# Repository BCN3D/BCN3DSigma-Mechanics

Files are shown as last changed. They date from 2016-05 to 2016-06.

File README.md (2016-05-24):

## What’s hold in this repository?
This repository will hold all the information about the Mechanics of the BCN3D Sigma.
As a declared Open Source organization, it's in our mission to release all the original design files to you to be able to learn, reuse and improve. Open Source not only means code, it also concerns hardware.

We’ve managed to design and manufacture the BCN3D Sigma thanks to our previous experience in the 3D printing industry, the ideas coming from the community, our engineering background and a narrow collaboration with our suppliers. Our goal is justify the decisions we took and share the know-how we acquired so far.

We also provide the source files for those who want to check the core of the BCN3D Sigma. You can consult both the CAD files and the technical drawings.

## CONCEPT DESIGN
During the concept design stage we set a clear target which determined the whole design and decisions: The BCN3D Sigma is a professional printer.

### Aesthetics
It has to look  like a professional equipment. Our previous printers were made with aluminium extruded profiles and plastic printed parts. That made sense for printers oriented to makers or schools, sold as a kit. But, in this case, aesthetic was a major player. For this reason, we adopted a welded aluminium frame, which allows the Sigma to be a unique and attractive 3D printer

### Multimaterial
As a professional printer, it has to print as many materials as possible. Not only for engineers, who require tough -or flexible-, functional polymers, but also for designers who need the aesthetic component. However, material is not the only limitation. Complex geometries, overhangs and 3D printing doesn’t get along. So we wanted the Sigma to be a real solution for those users who need to print with supports as a must. In conclusion, the Sigma is the first and only commercial 3D printer with an Independent Dual Extuder (IDEX) system, which avoid all the side problems dual extrusion may cause.

### High Quality
The 3D Printing industry is maturing. Users are more and more demanding and 3D printing must be a solution, not a headache. For this reason, the Sigma has to be a reliable piece of engineering, easy to assemble, maintain and capable to print seamlessly high quality objects, no matter how complex they are.

### High Capacity
Real-life and functional parts are not always small. A big printing volume is a great advantage for a professional 3D Printer although the Sigma intends to be a desktop-sized printer. Allocating all the items and devices inside the frame, while granting ease-to-use and optimizing the axes structure were a key goal.

## DETAIL DESIGN INSIGHTS

We faced dozens of challenges during the design process. Below we describe some of them:

### Frame
Probably the biggest challenge. First we thought in a chassis made of profiles and then cover it. But then realized the cost in materials for that solution would be high enough to look for alternatives that could contribute more in the aesthetic field, even that could be a bit more expensive. On the other side, we wanted the Sigma to be an accessible printer, wide and open in order to ease the handling and operation. So we decided to explore the option of designing a unibody frame where all the mechanical components were mounted on and with a wide frontal oberture.

First we had to decide between using aluminium or steel. Steel offers many advantages: It’s a very stiff metal, great to build structures and precise mechanical systems. In addition, it’s easy to work with and cheap. But it’s -really- heavy. We contemplated the option of using a thinner metal sheet of steel for the frame. After ordering a prototype, we dismissed the idea, though. Still it had a great mechanical behaviour and a relative low weight, the feeling of touching a thin metal sheet (1.5mm) was unpleasant because it felt like a cutting edge. And it didn’t look sturdy. So to achieve both a reliable look and a pleasant contact, we needed to go up to 3mm thickness. But then the shipping costs would be absurdly high and the handling, a constant hassle -both during the assembly process and for the final user.

Aluminium, on the other hand, provides lightness and a smooth and sturdy look. But it’s more expensive as a material and it’s harder to laser cut and weld. After balancing pros and cons, we bet on aluminium option -although we had a plan B.

The second big issue to manage was the manufacturing process. We contemplated two different ways to do it: either manufacture the frame by parts and screw them all together in the assembly line or weld the frame. Welding aluminium is hard and the welding process itself has some thermal and geometric implications that have to be considered. But it allows to reduce the assembling time dramatically while it outsources a key process.

As alternative, designing the frame as separate parts to screw together was considerably cheaper - as you save a handmade process such as welding and polishing. But the assembling of the frame and adjustment could be very delicate and incompatible with our production tag time. So the overall cost wouldn’t be that different in both options. The aesthetic component, though, would be very penalized with this alternative, because we would need to add dozens of screws on the frame.

For these reasons, we finally opted for a welded structure. We sat hours with our supplier discussing the best way to design every single part in order to grant a proper alignment between the faces that would hold the axes. Furthermore, we also studied the mechanical behaviour of the frame with some CAE studies, simulating stress and deformations during a standard usage.

### High quality components
A good frame is not enough to achieve amazing results. In such a precision equipment as the Sigma, all the mechanical components play a key role. Due to the product requirements in terms of size and use of the internal space of the printer we had, we opted for a axes structure with the toolheads moving in the XY plane and an up and down moving Z axis.

With the XY plane decided to mount high precision linear guides. Despite its cost slightly higher than a system based on rods and bearings, the linear rails offer a professional look, an easy assembling and a compact package.

Regarding the Z axis, we were aware of the importance to have a robust guide system in order to avoid classic artifacts in printed parts related with a bad Z performance, such as Z wobbling. We also had experience using couplings and to connect the actuator with the leadscrew and we knew that a bad assembling could cause poor quality results. With this background, we chose using Ø12mm guide rods and a stepper motor with an inserted leadscrew. The whole system provides a high repeatability and accuracy.

### Independent Dual Extrusion
A 3D printer with such an specific feature increases the design unknowns and multiplies the components. Not only the firmware and the electronics need to be highly customized, but also mechanically there are some decisions to take.

First of all, because of the multiple components to hold, the internal parts tend to be more complex than other printers. So we decided to use aluminium sheet bending technology to manufacture the inner parts. As the manufacturing tolerances are acceptable for the purposes we intend and the technology is cheap and easily scalable, we considered the technology optimum.  

Two independent Extruders means have an extra moving stepper for the second toolhead, and the extra toolhead itself. On the other hand, when printing with both extruders it’s important to have a bucket to purge the idle hotends before start printing the model again. All this parts add weight to a moving element, which is a problem to print fast because the high inertias may worsen the print quality. So we designed the X and Y Axis as light as possible, saving as many grams as possible with every single component. Not only weight is important when doubling the toolheads, but also space. So we decided to adopt a bowden-based feeding system and miniaturize all the items as much as possible.

### Big Printing Volume
The BCN3D Sigma features 210x297x210mm printing volume. In order to provide such a big volume and a free space on both sides to park the idle toolhead, but still having a desktop-sized printer, we had to reorient the Z platform. The main issue to solve, though, was granting the stiffness of the structure with a big overhang of more than 300mm.

To prevent vibrations, we adopted high quality bearings with low clearance and we designed and  simulated a custom metal sheet structure, which allows to get a great quality prints with a smooth surface despite the big overhang.

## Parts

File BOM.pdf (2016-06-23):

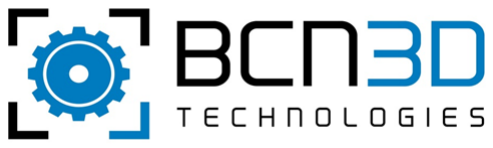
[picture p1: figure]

# | N/referencia S/referencia | Descripció | Unitats/kit | Proveïdor

1 | 10082 | CU03 | Cable USB 2.0 1,8m | 1 | CABLEMATIC
2 | 10210 | | SD Card 8GB | 1 | RS AMIDATA
3 | 10988 | | PLA 3mm 0,5kg JET BLACK STARTER KIT | 1 | BBOLID, S.L.
4 | 10989 | | PLA 3mm 0,5kg ARCTIC WHITE STARTER KIT | 1 | BBOLID, S.L.
5 | 10273 | FA80 | Cable alimentación IEC 1,5m | 1 | CABLEMATIC
6 | 10446 | Q34 | Pulley GT2, 20 Teeth 5mm Bore | 2 | JINAN YUKI INTERNATIONAL TRADE CO., LTD
7 | 10476 | | USB Cable Extension | 1
8 | 10616 | 145 | 3D Lac | 1 | LEÓN 3D IMPRESIÓN
9 | 10628 | P71 | Extruder Thermistor Wired | 2 | KUONGSHUN ELECTRONIC LIMITED
10 | 10826 | 15129 | Patas para tornillo 7,1x15,9mm | 4 | ESSENTRA COMPONENTS S.L.U
11 | 10827 | BCN3DSigma‐M01C00.0P000 | BCN3DSigma‐Structure | 1 | FARGUELL
12 | 10828 | BCN3DSigma‐M05C02.0P01D | BCN3DSigma‐Stepper Holder Right | 1 | FARGUELL
13 | 10829 | BCN3DSigma‐M05C01.0P02D | BCN3DSigma‐Stepper Holder Left | 1 | FARGUELL
14 | 10830 | BCN3DSigma‐M05C01.0P03D | BCN3DSigma‐X Axis Idler | 2 | FARGUELL
15 | 10831 | BCN3DSigma‐M05C01.0P01C | BCN3DSigma‐Belt Clamp | 2 | FARGUELL
16 | 10832 | | BCN3DSigma‐Upper Platform | 1 | FARGUELL
17 | 10833 | BCN3DSigma‐M03C01.0P01D | BCN3DSigma‐Lower Platform | 1 | FARGUELL
18 | 10834 | BCN3DSigma‐M03C01.0P02C | BCN3DSigma‐Reinforcement | 1 | FARGUELL
19 | 10835 | BCN3DSigma‐M06C01.0P05E | BCN3DSigma‐Lower Cover | 2 | FARGUELL
20 | 10836 | BCN3DSigma‐M06C01.0P06D | BCN3DSigma‐Upper Cover | 2 | FARGUELL
21 | 10837 | BCN3DSigma‐M06C01.0P07C | BCN3DSigma‐Hotend Plate | 2 | FARGUELL
22 | 10838 | BCN3DSigma‐M02C01.0P06B | BCN3DSigma‐Y Axis Idler | 2 | FARGUELL
23 | 10839 | BCN3DSigma‐M01C01.0P05C | BCN3DSigma‐Y Idler Tensioner | 2 | FARGUELL
24 | 10840 | BCN3DSigma‐M01C01.0P07B | BCN3DSigma‐Guide Spacer | 2 | FARGUELL
25 | 10841 | BCN3DSigma‐M01C01.0P15A | BCN3DSigma‐Square 90 | 8 | RIERA I TUTÓ
26 | 10842 | BCN3DSigma‐M01C01.0P16A | BCN3DSigma‐Square 60 | 2 | RIERA I TUTÓ
27 | 10843 | BCN3DSigma‐M04C02.0P01C | BCN3DSigma‐SD Holder | 1 | FARGUELL
28 | 10844 | BCN3DSigma‐M04C01.0P02B | BCN3DSigma‐Screen Bezel | 1 | FARGUELL
29 | 10845 | BCN3DSigma‐M08C01.0P02A | BCN3DSigma‐Spool Support | 2 | FARGUELL
30 | 10846 | BCN3DSigma‐M05C03.0P02A | BCN3DSigma‐X Support | 2 | FARGUELL
31 | 10847 | BCN3DSigma‐M05C03.0P03A | BCN3DSigma‐Connection plate | 2 | FARGUELL
32 | 10848 | BCN3DSigma‐M05C03.0P01A | BCN3DSigma‐X Reinforcement | 1 | FARGUELL
33 | 10849 | BCN3DSigma‐M05C01.0P06C | BCN3DSigma‐Purger Base Left | 1 | FARGUELL
34 | 10850 | BCN3DSigma‐M05C02.0P02C | BCN3DSigma‐Purger Base Right | 1 | FARGUELL
35 | 10851 | BCN3DSigma‐M06C01.0P08D | BCN3DSigma‐X Plate Left | 1 | FARGUELL
36 | 10852 | BCN3DSigma‐M06C02.0P01D | BCN3DSigma‐X Plate Right | 1 | FARGUELL
37 | 10853 | BCN3DSigma‐M06C01.0P04C | BCN3DSigma‐Connection Board Support | 2 | FARGUELL
38 | 10854 | BCN3DSigma‐M02C02.0P01C | BCN3DSigma‐Y Stepper Holder | 1 | FARGUELL
39 | 10855 | BCN3DSigma‐M07C01.0P05C | BCN3DSigma‐Extruder Stepper Holder | 2 | FARGUELL
40 | 10856 | BCN3DSigma‐M07C01.0P03A | BCN3DSigma‐Extruder Plate MK8 | 2 | FARGUELL
41 | 10857 | VIDRIO MATE 4, 212X300mm | Vidrio Mate 4, 212x300mm, 0,5mm canto biselado | 1 | DISOLGLASS, S.L.
42 | 10858 | FFC1.00A15/1151M4.0‐4.0‐08.0‐0 | BCN3DSigma‐Cable FFC X1 Motor | 1 | AXON' CABLE S.A.S.
43 | 10859 | FFC1.00A15/1151M4.0‐4.0‐08.0‐0 | BCN3DSigma‐Cable FFC X0 Motor | 1 | AXON' CABLE S.A.S.
44 | 10860 | FFC1.00A15/0159M4.0‐4.0‐08.0‐0 | BCN3DSigma‐Cable FFC Z Motor | 1 | AXON' CABLE S.A.S.
45 | 10861 | FFC1.00A15/0750M4.0‐4.0‐08.0 | BCN3DSigma‐Cable FFC Y Motor | 1 | AXON' CABLE S.A.S.
46 | 10862 | FFC1.00A15/0561M4.0‐4.0‐08.0 | BCN3DSigma‐Cable FFC Extruder 1 | 1 | AXON' CABLE S.A.S.
47 | 10863 | FFC1.00A15/0561M4.0‐4.0‐08.0 | BCN3DSigma‐Cable FFC Extruder 0 | 1 | AXON' CABLE S.A.S.
48 | 10864 | FFC1.00D20/1439M5.0‐5.0‐08.0 | BCN3DSigma‐Cable FFC Hotend 0 | 1 | AXON' CABLE S.A.S.
49 | 10865 | FFC1.00D20/1439M5.0‐5.0‐08.0 | BCN3DSigma‐Cable FFC Hotend 1 | 1 | AXON' CABLE S.A.S.
50 | 10866 | BCN3DSigma‐M09C00.0P09B | BCN3DSigma‐Cable Hotbed | 1 | CHANGZHOU SMART AUTOMATION MOTOR MANUFACTURING CO., LTD.
51 | 10867 | BCN3DSigma‐M09C00.0P10B | BCN3DSigma‐Cable Power AC | 1 | CHANGZHOU SMART AUTOMATION MOTOR MANUFACTURING CO., LTD.
52 | 10868 | BCN3DSigma‐M09C00.0P11A | BCN3DSigma‐Cable Power DC | 1 | CHANGZHOU SMART AUTOMATION MOTOR MANUFACTURING CO., LTD.
53 | 10869 | BCN3DSigma‐M09C00.0P12B | BCN3DSigma‐Cable LCD | 1 | CHANGZHOU SMART AUTOMATION MOTOR MANUFACTURING CO., LTD.
54 | 10870 | BCN3DSigma‐M09C00.0P13C | BCN3DSigma‐Cable LED | 2 | CHANGZHOU SMART AUTOMATION MOTOR MANUFACTURING CO., LTD.
55 | 10871 | BCN3DSigma‐M09C00.0P14C | BCN3DSigma‐Cable Endstop Y | 1 | CHANGZHOU SMART AUTOMATION MOTOR MANUFACTURING CO., LTD.
56 | 10872 | BCN3DSigma‐M09C00.0P15A | BCN3DSigma‐Cable Endstop X | 2 | CHANGZHOU SMART AUTOMATION MOTOR MANUFACTURING CO., LTD.
57 | 10873 | BCN3DSigma‐M09C00.0P16B | BCN3DSigma‐Cable Endstop Z | 2 | CHANGZHOU SMART AUTOMATION MOTOR MANUFACTURING CO., LTD.
58 | 10874 | BCN3DSigma‐M09C00.0P17A | BCN3DSigma‐Cable SD | 1 | CHANGZHOU SMART AUTOMATION MOTOR MANUFACTURING CO., LTD.
59 | 10875 | MGN9H rail 360mm+1 block | MGN9H rail 360 mm + 1 MGN9H block | 2 | JINAN YUKI INTERNATIONAL TRADE CO., LTD
60 | 10876 | MGN9H rail 432mm + 2 block | MGN9H rail 432mm + 2 MGN9H block | 1 | JINAN YUKI INTERNATIONAL TRADE CO., LTD
61 | 10877 | LMF12UU Linear bearing | LMF12UU Linear bearing | 2 | JINAN YUKI INTERNATIONAL TRADE CO., LTD
62 | 10878 | SK12 Shaft Support | SK12 Shaft Support | 4 | JINAN YUKI INTERNATIONAL TRADE CO., LTD
63 | 10879 | KFL08 Bearing Pillow Block | KFL08 Bearing Pillow Block | 2 | JINAN YUKI INTERNATIONAL TRADE CO., LTD
64 | 10880 | GT2 Belt 6mm closed belt 810mm | GT2 Belt 6mm width closed belt 810mm | 2 | KUONGSHUN ELECTRONIC LIMITED
65 | 10881 | GT2 Belt 6mm closed belt 782mm | GT2 Belt 6mm width closed belt 782mm | 2 | KUONGSHUN ELECTRONIC LIMITED

SIGMA Escandall 31 Març 2016

66 | 10882 | GT2 Belt 12mm closed belt 112m | GT2 Belt 12mm width closed belt 112mm | 1 | KUONGSHUN ELECTRONIC LIMITED
67 | 10883 | GT2 Pulley20 teeth 8mm bore 12 | GT2 Pulley 20 teeth 8mm bore for 12mm width belt | 1 | JINAN YUKI INTERNATIONAL TRADE CO., LTD
68 | 10884 | GT2 Pulley20 teeth 5mm bore 12 | GT2 Pulley 20 teeth 5mm bore for 12mm width belt | 1 | JINAN YUKI INTERNATIONAL TRADE CO., LTD
69 | 10885 | GT2 Pulley 20 teeth 8mm bore 6 | GT2 Pulley 20 teeth 8mm bore for 6mm width belt | 6 | JINAN YUKI INTERNATIONAL TRADE CO., LTD
70 | 10886 | MR105zz | Ball Bearing MR105zz | 2 | JINAN YUKI INTERNATIONAL TRADE CO., LTD
71 | 10887 | RSP‐320‐24 | Power Supply 24V 320W | 1 | OLFER
72 | 10888 | ULM 06110‐05 | High Knurled Knut DIN 466 M5 | 2 | UTILNORM, S.L
73 | 10889 | 06094‐004 | Botón moleteado con rosca interior | 2 | UTILNORM, S.L
74 | 10890 | BCN3DSigma‐M01C02.0P01B | BCN3DSigma‐Inner covers PS blau | 1 | GLAS FORM S.L.
75 | 10891 | BCN3DSigma‐M01C02.0P02B | BCN3DSigma‐Electronics cover PS blau | 1 | GLAS FORM S.L.
76 | 10892 | BCN3DSigma‐M01C02.0P03A | BCN3DSigma‐LCD cover PS blau | 1 | GLAS FORM S.L.
77 | 10893 | BCN3DSigma‐M01C03.0P01B | BCN3DSigma‐Bottom cover PS negre 1mm | 1 | GLAS FORM S.L.
78 | 10894 | BCN3DSigma‐M01C01.0P08B | BCN3DSigma‐Window PET‐G 2mm incoloro | 2 | FERPLAST, S.L.
79 | 10895 | M03C02.0P04Z | Muelle 15,75xINT=5,7x1:E7 AMOLADO | 3 | MUELLES Y RESORTES BOSCH, S.L.
80 | 10896 | M07C00.0P13Z | Muelle 25,4xINT=3,96X1,1:E:14,5 AMOLADO | 2 | MUELLES Y RESORTES BOSCH, S.L.
81 | 10897 | Q99 PTFE Teflon Tube, ID=4mm | PTFE Teflon Tube, ID=4mm OD=6mm [m] | 1 | KUONGSHUN ELECTRONIC LIMITED
82 | 10898 | BCN3DSigma‐M02C01.0P04A | BCN3D Sigma‐Y Transmision bar | 1 | MECANIZADOS CHAVES S.C.P.
83 | 10899 | BCN3DSigma‐M02C02.0P02B | BCN3DSigma‐Y Belt tensor | 1 | MECANIZADOS CHAVES S.C.P.
84 | 10900 | BCN3DSigma‐M06C03.0P03A | BCN3DSigma‐Hot block | 2 | MECANIZADOS CHAVES S.C.P.
85 | 10901 | SM35HT36‐1004A | SM35HT36‐1004A (Nema 14 36mm) | 2 | CHANGZHOU SMART AUTOMATION MOTOR MANUFACTURING CO., LTD.
86 | 10903 | Z Motor + Nut | SM42HT33‐1334L with Tr8*2 260mm length + nut | 1 | CHANGZHOU SMART AUTOMATION MOTOR MANUFACTURING CO., LTD.
87 | 10904 | SM42HT60‐1684A | SM42HT60‐1684A (Nema 17 60mm) | 2 | CHANGZHOU SMART AUTOMATION MOTOR MANUFACTURING CO., LTD.
88 | 10905 | BCN3DSigma‐M03C01.0P03B | BCN3D Sigma‐Z Bar | 2 | MECANIZADOS CHAVES S.C.P.
89 | 10906 | BCN3DSigma‐M03C02.0P02B Cork | Hotbed cork 297x210x3 mm corcho aglomerado | 1 | BARNACORK S.L.
90 | 10907 | BCN3DSigma‐M04C00.0P03A | Stepper Driver | 6 | TEF MONTAJES Y SERVICIOS, S.L.
91 | 10908 | BCN3DSigma‐M03C02.0P05A | Heated Bed | 1 | TEF MONTAJES Y SERVICIOS, S.L.
92 | 10909 | BCN3DSigma‐M04C00.0P02A | Mother Board | 1 | TEF MONTAJES Y SERVICIOS, S.L.
93 | 10910 | BCN3DSigma‐M04C00.0P04A | Extruder Board | 2 | TEF MONTAJES Y SERVICIOS, S.L.
94 | 10911 | BCN3DSigma‐M06C03.0P02A | BCN3DSigma‐Heatbreak | 2 | MECANIZADOS CHAVES S.C.P.
95 | 10912 | BCN3DSigma‐M06C03.0P04B | BCN3DSigma‐Heatsink | 2 | MECANIZADOS CHAVES S.C.P.
96 | 10913 | BCN3DSigma‐M07C00.0P01B | BCN3DSigma‐Extruder Clamp MK8 | 2 | MECANIZADOS CHAVES S.C.P.
97 | 10914 | BCN3DSigma‐M07C00.0P02B | BCN3DSigma‐Extruder Holder MK8 | 2 | MECANIZADOS CHAVES S.C.P.
98 | 10915 | BCN3DSigma‐M05C01.0P07A Silico | Silicone Cloth Pieza 36x13x2 mm silicona | 2 | I.M.C. esquerda S.L.
99 | 10916 | AV‐F4020HB | Axial fan 4010 24V 130mm PHR 2 | 2 | SHENZHEN XINYUJIE TECHNOLOGY CO., LTD
100 | 10917 | XJ24B3010H | DC axial fan 3010 24V, PHR2 85mm | 2 | SHENZHEN XINYUJIE TECHNOLOGY CO., LTD
101 | 10918 | BCN3DSigma‐M07C01.0P06B | BCN3DSigma‐Extruder driver cover | 2 | FARGUELL
102 | 10919 | NA009 | Neodimio Aro 9.5‐5.5‐2 | 3 | AIMAN G Z, S.L.
103 | 10920 | NE006 | Neodimio Esfera 6 | 3 | AIMAN G Z, S.L.
104 | 10921 | uLCD‐35DT‐AR 4D Systems | Pantalla uLCD‐35DT‐AR 4D Systems | 1 | RS AMIDATA
105 | 10922 | BCN3DSigma‐M07C01.0P04B | Pneufit Coupling | 4 | RAMON CASADO
106 | 10923 | BCN3DSigma‐M06C03.0P01A | NOZZLE 0,4mm SIGMA | 2 | RAMON CASADO
107 | 10924 | White bowden tube clamp Blue h | Coupling collet | 4
108 | 10925 | P70 24V40W Reprap Cartridge He | Cartridge Heater 24 V 40W | 2 | KUONGSHUN ELECTRONIC LIMITED
109 | 10926 | 682‐2657 | SS‐5‐FD MICROSWITCH, 5A, PIN, SPDT, SOLDER | 5 | RS AMIDATA
110 | 10927 | Led strip RGB 5050 5m roll, 24 | Led strip RGB 5050 5m roll, 24V, NO waterproof | 0,13 | KUONGSHUN ELECTRONIC LIMITED
111 | 10928 | 18B304 | Espátula 40mm | 1 | ALBIMAR
112 | 10929 | Cojinete selfoil A.04.08.08 | Casquillo selfoil 4‐8‐8 | 8 | IBERMETAL
113 | 10930 | 102‐6110 | Espaciador Redondo, Poliamida, negro 3,2x6x3 | 14 | RS AMIDATA
114 | 10931 | N‐5E | Nylon UL94 V2 6/6, RMS‐01 | 2 | ESSENTRA COMPONENTS S.L.U
115 | 10933 | 460293 | Prensacables Adhesivos Planos | 13 | RS AMIDATA
116 | 10934 | 39D773 | Tornavis estrella PH0X50 | 1 | ALBIMAR
117 | 10935 | 741‐0912 | Interruptor de balancín, 1881.1103 | 1 | RS AMIDATA
118 | 10936 | 541‐4533 | Fusible 250V 10A 5x20mm | 2 | RS AMIDATA
119 | 10938 | 239‐4600 | Cinta adhesiva Advance Tapes 205882 Blanco Mate [m] | 1,4 | RS AMIDATA
120 | 10939 | 32D726 | Alicates 140mm C/Muelle | 1 | ALBIMAR
121 | 10956 | BCN3DSigma‐M05C01.0P12B | BCN3DSigma‐X Stepper Driver Holder Left | 1 | FARGUELL
122 | 10957 | BCN3DSigma‐M05C02.0P04B | BCN3DSigma‐X Stepper Driver Holder Right | 1 | FARGUELL
123 | 10959 | RPT117 | Caixa petita sigma | 1 | RAJAPACK
124 | 10964 | | Llave Allen P/Bola Pavonada 1,5mm | 1 | ALBIMAR
125 | 10965 | | Llave Allen P/Bola Pavonada 2,55mm | 1 | ALBIMAR
126 | 10966 | | Llaven Allen P/Bola Pavonada 4mm | 1 | ALBIMAR
127 | 10967 | A.03.06.06 | Casquillo selfoil A‐3‐6‐6 | 2 | ALUMINIOS Y PLASTICOS CATALUÑA
128 | 10970 | MK8 Drive Gear | MK8 Drive Gear | 2 | REPRAP.ME
129 | 10971 | FP38330 | Selfoil Tipo B con valona 3.6.10 9‐1,4 | 2 | RATIONAL STOCK
130 | 10972 | FP38329 | Selfoil Tipo B con valona 3.6.5 9‐1,5 | 2 | RATIONAL STOCK
131 | 10973 | SD‐uSD reader | SD Module | 1 | KUONGSHUN ELECTRONIC LIMITED
132 | 10991 | 188‐9618 | Conector filtro IEC950 FN9260‐2‐06 | 1 | RS AMIDATA
133 | 10976 | | Conjunto protección Sigma | 1 | BRAFIM
134 | 10978 | 758‐2593 | Tarjeta Memoria Flash Micro SDHC 4GB, C4 | 1 | RS AMIDATA
135 | 10982 | 4100318159 | PTFE tube ID1/8” x OD1/4” [m] | 1,80 | Polyflon Technology Limited
136 | 10983 | BCN3DSigma‐M03C03.0P02A | BCN3DSigma‐Z Stepper Holder | 1 | FARGUELL
137 | 10984 | SIGMA CE Label BCN3D Sigma Label Crush Label Thumbscrew Label Hot surface Label | Etiquetas | 1 | GAM DIGITAL
138 | 10985 | | Caixa exterior sigma 4 solapas | 1 | FLAK SL.
139 | 10986 | | Idler Pulley Shaft | 4 | MECANIZADOS CHAVES S.C.P.
140 | 10987 | SM42HT47‐1684A | SM42HT47‐1684A (nema 17 42mm) | 1 | CHANGZHOU SMART AUTOMATION MOTOR MANUFACTURING CO., LTD.
141 | 11001 | Etiquetas SIGMA BCN3D | BCN3D SIGMA Logo | 1 | GRAMAGRAF SCCL
142 | 11002 | Etiquetas SIGMA CE Label | SIGMA Label CE | 2 | GRAMAGRAF SCCL
143 | 11003 | Etiquetas Crush Label | Warning Hand Injury Label | 1 | GRAMAGRAF SCCL
144 | 11004 | Etiquetas Hot Surface Label | Hot Surface Label | 2 | GRAMAGRAF SCCL
145 | 11005 | 4787‐612 24316/P | Bandeja Sigma troquelada (13+1) | 1 | FLAK S.L.
146 | 11006 | ADHESIVO_TUERCA | adhesivo tuerca Sigma | | GRAMAGRAF SCCL
147 | 11007 | cartolina kraft 300gr. Troquel | Troquel Draudi | 1 | GAM DIGITAL
148 | | | Conjunto tornillería Sigma | 1 | RATIONAL STOCK

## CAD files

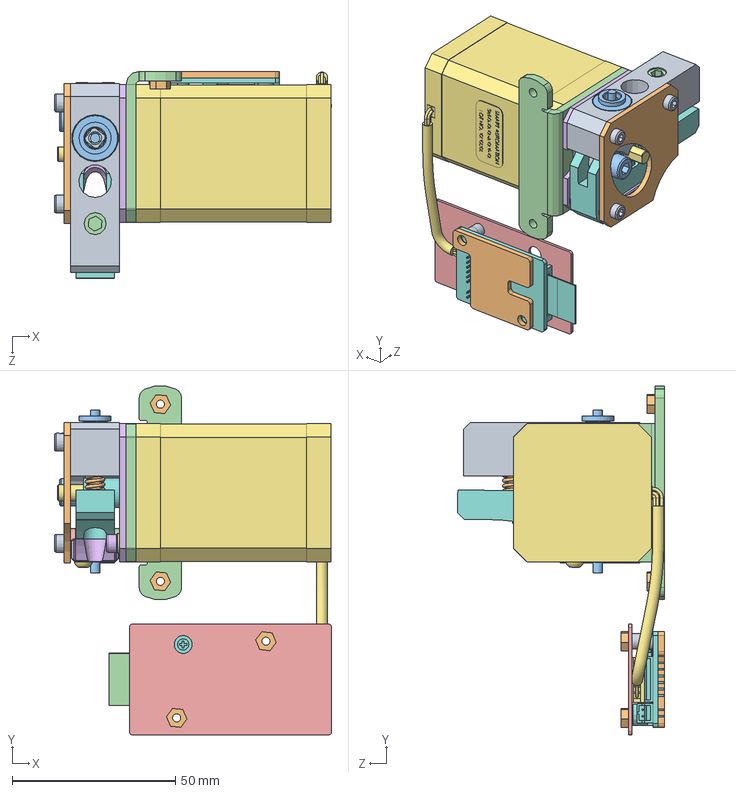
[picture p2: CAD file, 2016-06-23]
CAD/BCN3DSigma-M07C01.0P000 Left extruder.SLDASM
85.0 x 107.0 x 63.5 mm
DIN912 M3x25 x 3
DIN934 M3 x 4
DIN912 M5x12
DIN913 M8x6
DIN913 M3x3
DIN912 M3x8
BCN3DSigma-M07C01.0P01C Extruder clamp MK8
BCN3DSigma-M07C01.0P02D Extruder Holder MK8
BCN3DSigma-M07C01.0P03A Extruder plate MK8
BCN3DSigma-M07C01.0P04C Pneufit coupling
BCN3DSigma-M07C01.0P05C Extruder Stepper Holder
BCN3DSigma-M07C01.0P06B Extruder driver cover
BCN3DSigma-M07C01.0P08C Bowden entry extruder
BCN3DSigma-M07C01.0P10Z Nema 17 60mm
BCN3DSigma-M07C01.0P11Z Direct Drive Gear MK8
BCN3DSigma-M07C01.0P12Z Bearing 10-5-4
BCN3DSigma-M07C01.0P13A Extruder spring
BCN3DSigma-M07C01.0P19Z Coupling collet
BCN3DSigma-M07C01.0P15Z Bushing 3-6-10-1.5
BCN3DSigma-M07C01.0P16Z Bushing 3-6-5-1.5
BCN3DSigma-M07C01.0P17C Stepper insulator
BCN3DSigma-M07C01.0P18Z Clamp stop bushing
BCN3DSigma-M04C00.0P03E Stepper Driver Board
BCN3DSigma-M04C00.0P05Z Plastic spacer 3,2mm x 4
BCN3DSigma-M05C01.0P11B Driver spacer
Connexio cable pla 15 vies

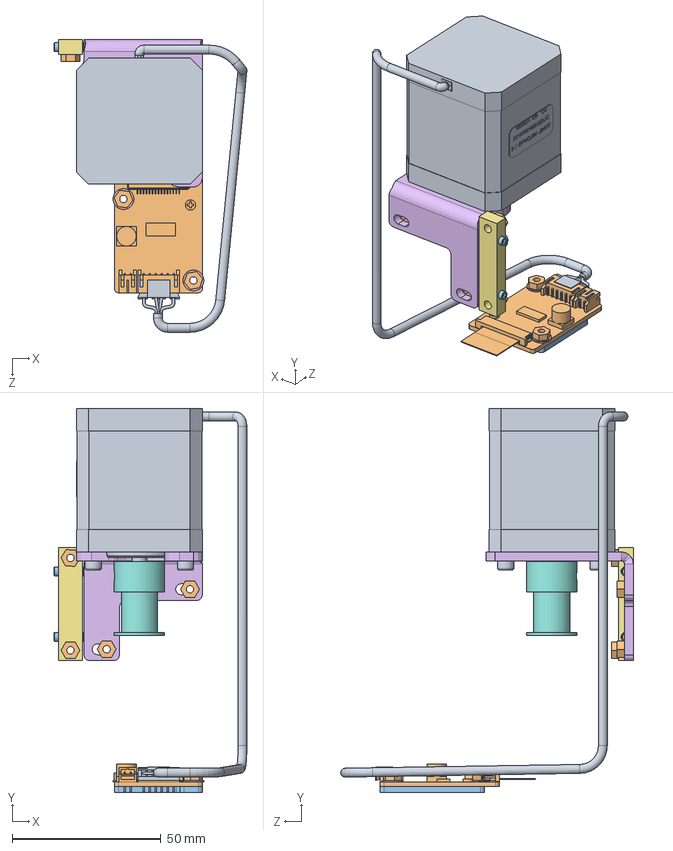
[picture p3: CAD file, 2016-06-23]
CAD/BCN3DSigma-M02C02.0P000 Y Motor.SLDASM
64.8 x 128.9 x 98.3 mm
DIN912 M3x10 x 3
DIN934 M3 x 6
DIN 913 M3x10 x 2
DIN913 M4x3 x 2
DIN125 M3 poliamida x 2
BCN3DSigma-M02C02.0P01C Y Stepper Holder
BCN3DSigma-M02C02.0P02C Y Belt tensor
BCN3DSigma-M02C02.0P04Z GT2 Pulley Ø5mm Bore 12mm width
BCN3DSigma-M02C02.0P06Z Nema17 47mm
BCN3DSigma-M04C00.0P03E Stepper Driver Board
BCN3DSigma-M05C01.0P11B Driver spacer

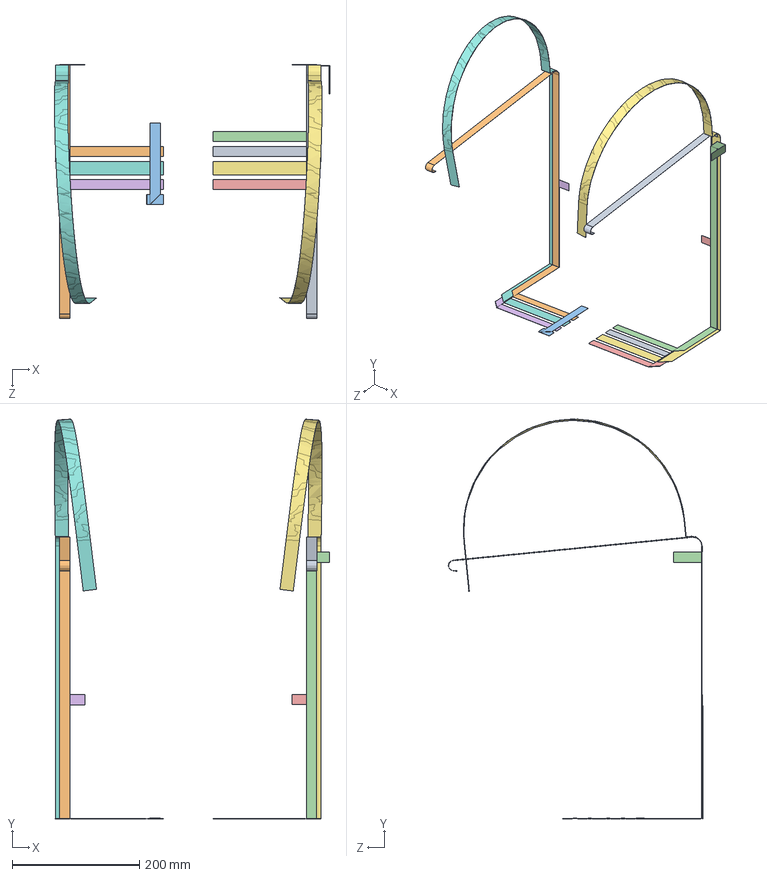
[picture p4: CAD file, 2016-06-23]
CAD/BCN3DSigma-M09C00.0P000 Wiring.SLDASM
432.5 x 628.7 x 399.5 mm
BCN3DSigma-M09C00.0P01A FFC X1 stepper
BCN3DSigma-M09C00.0P02A FFC X0 stepper
BCN3DSigma-M09C00.0P03A FFC Z stepper
BCN3DSigma-M09C00.0P04A FFC Y stepper
BCN3DSigma-M09C00.0P05A FFC Extruder 1
BCN3DSigma-M09C00.0P06A FFC Extruder 0
BCN3DSigma-M09C00.0P08A FFC Hotend 1
BCN3DSigma-M09C00.0P07A FFC Hotend 0

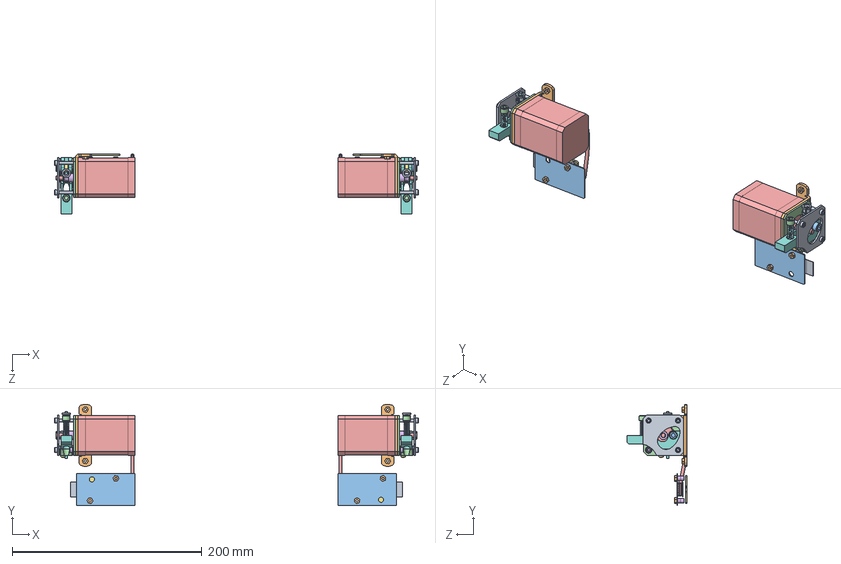
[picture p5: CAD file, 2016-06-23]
CAD/BCN3DSigma-M07C00.0P000 Extruders MK8.SLDASM
384.1 x 107.0 x 63.7 mm
DIN912 M3x25 x 6
DIN934 M3 x 8
DIN912 M5x12 x 2
DIN913 M8x6 x 2
DIN913 M3x3 x 2
DIN912 M3x8 x 2
BCN3DSigma-M07C01.0P01C Extruder clamp MK8 x 2
BCN3DSigma-M07C01.0P03A Extruder plate MK8 x 2
BCN3DSigma-M07C01.0P05C Extruder Stepper Holder x 2
BCN3DSigma-M07C01.0P06B Extruder driver cover x 2
BCN3DSigma-M07C01.0P08C Bowden entry extruder x 2
BCN3DSigma-M07C01.0P10Z Nema 17 60mm x 2
BCN3DSigma-M07C01.0P11Z Direct Drive Gear MK8 x 2
BCN3DSigma-M07C01.0P12Z Bearing 10-5-4 x 2
BCN3DSigma-M07C01.0P13A Extruder spring x 2
BCN3DSigma-M07C01.0P19Z Coupling collet x 2
BCN3DSigma-M07C01.0P15Z Bushing 3-6-10-1.5 x 2
BCN3DSigma-M07C01.0P16Z Bushing 3-6-5-1.5 x 2
BCN3DSigma-M07C01.0P17C Stepper insulator x 2
BCN3DSigma-M07C01.0P18Z Clamp stop bushing x 2
BCN3DSigma-M04C00.0P05Z Plastic spacer 3,2mm x 8
BCN3DSigma-M05C01.0P11B Driver spacer x 2
Connexio cable pla 15 vies x 2
ISO7380 M3x10

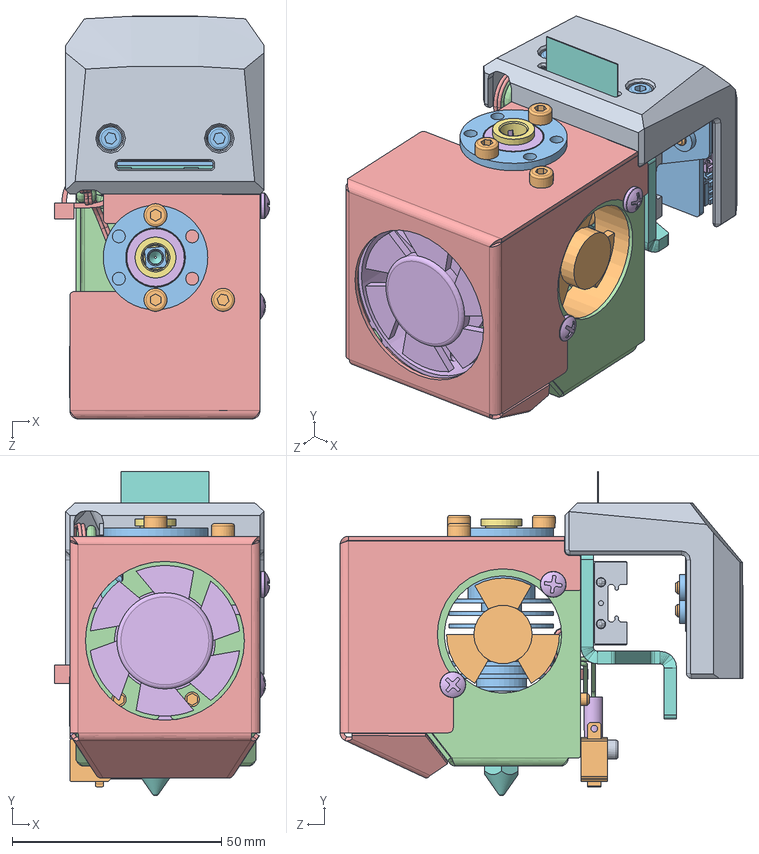
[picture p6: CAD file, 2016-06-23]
CAD/BCN3DSigma-M06C02.0P000 Right Hotend.SLDASM
51.5 x 77.5 x 96.3 mm
DIN912 M2,5x10 x 2
DIN912 M3x6 x 9
DIN912 M3x8 x 4
DIN912 M3x18 x 3
DIN7991 M3x10 x 2
DIN7981 9.5x3.2 x 2
DIN125 M3 poliamida x 4
BCN3DSigma-M06C02.0P01E X Plate Right
BCN3DSigma-M06C01.0P01D Conexion cover
BCN3DSigma-M06C01.0P03Z Heat sink fan
BCN3DSigma-M06C01.0P04C Connection board support
BCN3DSigma-M06C01.0P05E Lower cover
BCN3DSigma-M06C01.0P06D Upper cover
BCN3DSigma-M06C01.0P09Z Layer fan
BCN3DSigma-M06C01.0P11B Cable clip
BCN3DSigma-M06C01.0P12B Layer fan spacer
BCN3DSigma-M06C01.0P13A Flat cable clip
BCN3DSigma-M02C01.0P08Z Endstop
BCN3DSigma-M04C00.0P04A Hotend Board
BCN3DSigma-M09C00.0P16B Endstop Z Right
BCN3DSigma-M09C00.0P20A Zip tie
BCN3DSigma-M09C00.0P21A Enstop shrink tube x 2
DIN913 M3x3 x 2
BCN3DSigma-M06C03.0P01B Nozzle 0.4
BCN3DSigma-M06C03.0P02A Heatbreak
BCN3DSigma-M06C03.0P03A Hot block
BCN3DSigma-M06C03.0P04D Heatsink bowden
BCN3DSigma-M06C03.1P01A Resistance 24V
BCN3DSigma-M06C03.1P02A Thermistor
BCN3DSigma-M07C01.0P04C Pneufit coupling
BCN3DSigma-M07C01.0P19Z Coupling collet
Connexio cable pla hotend
Linear guide slide
BCN3DSigma-M06C01.0P14A Hot surface Label

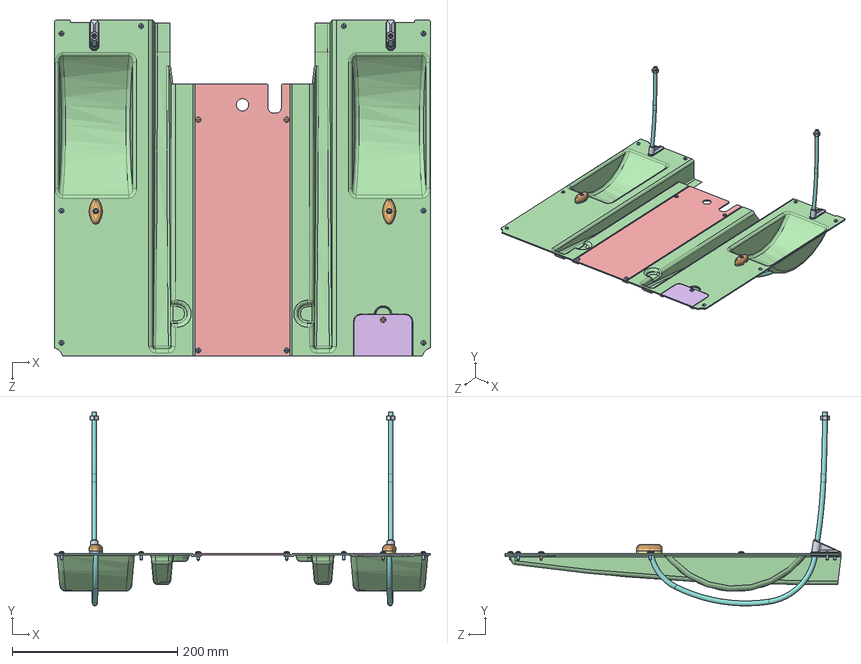
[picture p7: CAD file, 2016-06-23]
CAD/BCN3DSigma-M01C02.0P000 Structure covers.SLDASM
455.4 x 234.6 x 407.0 mm
DIN934 M6 x 2
DIN7981 3.2x9.5 x 3
DIN7985 M3x8 x 10
BCN3DSigma-M01C02.0P01D Inner cover
BCN3DSigma-M01C02.0P02D Electronics cover
BCN3DSigma-M01C02.0P03A LCD cover
BCN3DSigma-M01C02.0P04B Bowden entry bottom right
BCN3DSigma-M01C02.0P05C Extruder entry bowden x 2
BCN3DSigma-M01C02.0P06C Bowden entry guide x 2
BCN3DSigma-M01C02.0P07A Bowden entry top x 2
BCN3DSigma-M01C02.0P08A Bowden entry bottom left

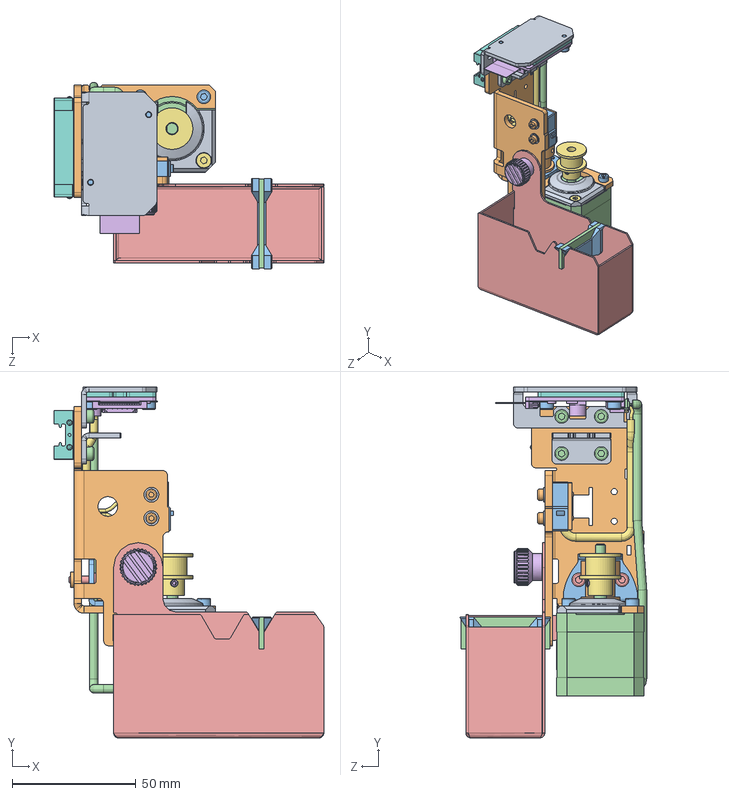
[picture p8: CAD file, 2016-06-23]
CAD/BCN3DSigma-M05C01.0P000 X Axis Left.SLDASM
109.0 x 141.9 x 75.4 mm
DIN125 M2,5 x 2
DIN912 M2,5x12 x 2
DIN912 M3x6 x 7
DIN912 M3x8 x 4
DIN912 M3x10 x 2
DIN913 M3x3 x 2
DIN7991 M3x6
DIN125 M3 poliamida x 2
BCN3DSigma-M05C01.0P01C Belt Clamp
BCN3DSigma-M05C01.0P02E Stepper Holder Left
BCN3DSigma-M05C01.0P03D X Axis Idler
BCN3DSigma-M05C01.0P5Z Nema 14
BCN3DSigma-M05C01.0P06C Purger Base Left
BCN3DSigma-M05C01.0P08Z Purger Button
BCN3DSigma-M05C01.0P15Z GT2 Pulley Ø5mm Bore 6mm width
BCN3DSigma-M05C01.0P11B Driver spacer
BCN3DSigma-M05C01.0P12B X Stepper Driver Holder Left
BCN3DSigma-M02C01.0P13Z GT2 Pulley Ø8mm Bore 6mm width
BCN3DSigma-M02C01.0P08Z Endstop
BCN3DSigma-M02C01.0P10A Idler pulley shaft
BCN3DSigma-M02C01.0P11Z Pulley bushing 4-8-8 x 2
BCN3DSigma-M04C00.0P03E Stepper Driver Board
BCN3DSigma-M09C00.0P15A Endstop X Left
Linear guide slide
BCN3DSigma-M05C01.0P04B Stepper cover left
BCN3DSigma-M05C01.0P16A Endstop Threaded Plate
BCN3DSigma-M05C01.0P14A Cloth Support
BCN3DSigma-M05C01.0P07A Silicone Cloth

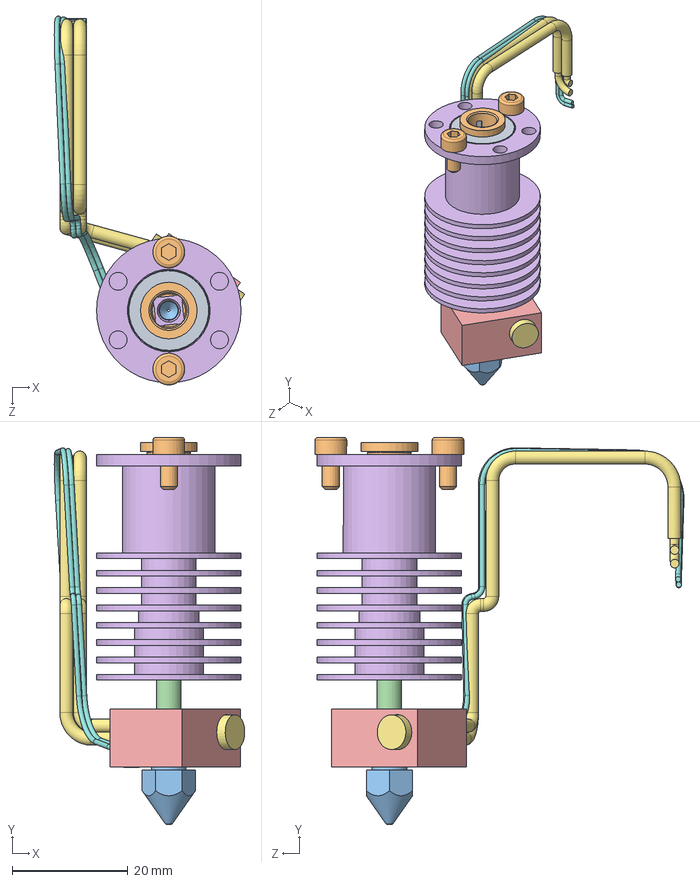
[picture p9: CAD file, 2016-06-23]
CAD/BCN3DSigma-M06C03.0P000 Hotend.SLDASM
32.9 x 67.0 x 63.8 mm
DIN913 M3x3 x 2
DIN912 M3x6 x 2
BCN3DSigma-M06C03.0P01B Nozzle 0.4
BCN3DSigma-M06C03.0P02A Heatbreak
BCN3DSigma-M06C03.0P03A Hot block
BCN3DSigma-M06C03.0P04D Heatsink bowden
BCN3DSigma-M06C03.1P01A Resistance 24V
BCN3DSigma-M06C03.1P02A Thermistor
BCN3DSigma-M07C01.0P04C Pneufit coupling
BCN3DSigma-M07C01.0P19Z Coupling collet

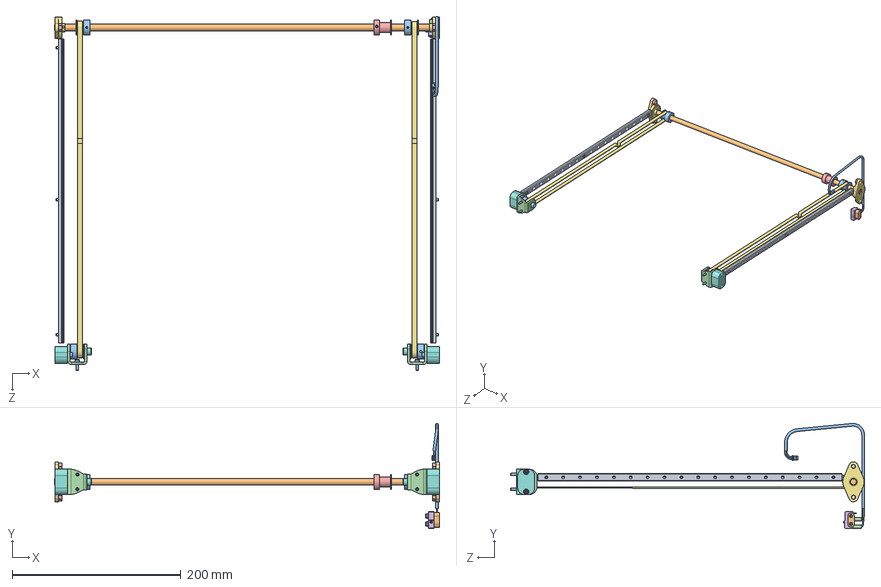
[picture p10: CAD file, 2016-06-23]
CAD/BCN3DSigma-M02C01.0P000 Transmision Y Axis.SLDASM
456.0 x 124.6 x 419.4 mm
DIN985 M2.5 x 2
DIN912 M3x6 x 6
DIN912 M3x10 x 8
DIN913 M3x3 x 4
DIN934 M5 x 4
DIN913 M4x3 x 2
BCN3DSigma-M02C01.0P01Z Bearing Pillow Block x 2
BCN3DSigma-M02C01.0P02C Idler Spacer x 2
BCN3DSigma-M02C01.0P03Z Y Guide x 2
BCN3DSigma-M02C01.0P04A Transmission Bar
BCN3DSigma-M02C01.0P05Z GT2 Pulley Ø8mm Bore 6mm width x 4
BCN3DSigma-M02C01.0P06C Y Axis Idler x 2
BCN3DSigma-M02C01.0P07Z GT2 Pulley Ø8mm Bore 12mm Width
BCN3DSigma-M02C01.0P08Z Endstop
BCN3DSigma-M02C01.0P09Z Y Belt x 2
BCN3DSigma-M02C01.0P10A Idler pulley shaft x 2
BCN3DSigma-M02C01.0P11Z Pulley bushing 4-8-8 x 4
BCN3DSigma-M02C01.0P12A Y Endstop spacer
BCN3DSigma-M09C00.0P14B Y Endstop cable
BCN3DSigma-M09C00.0P21A Enstop shrink tube x 2

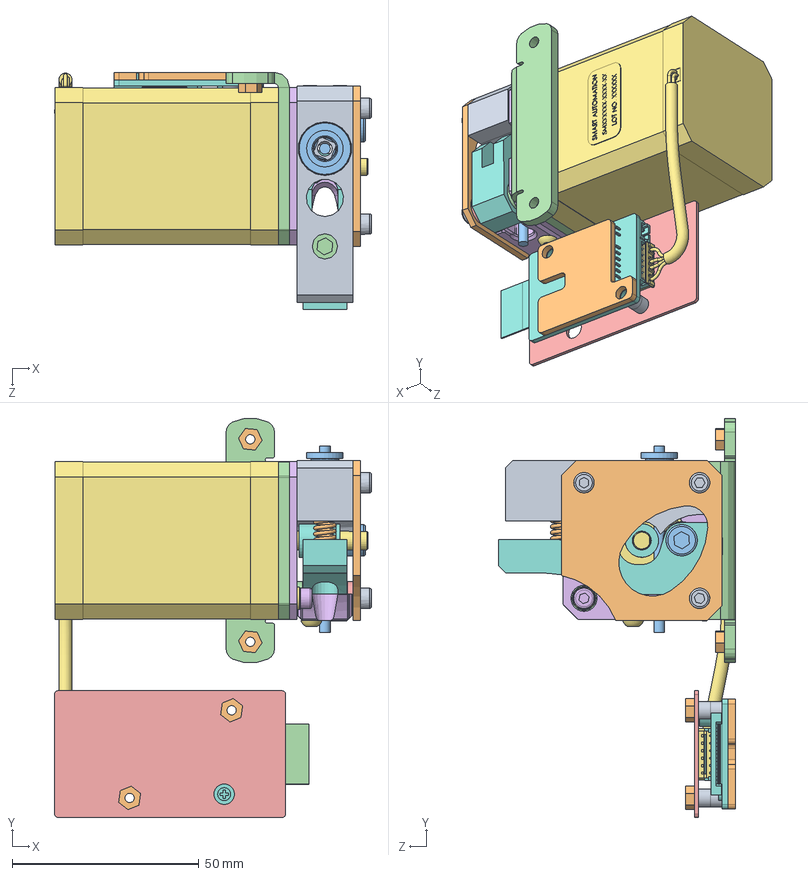
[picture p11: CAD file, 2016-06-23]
CAD/BCN3DSigma-M07C02.0P000 Right extruder.SLDASM
85.0 x 107.0 x 63.6 mm
DIN912 M3x25 x 3
DIN934 M3 x 4
DIN912 M5x12
DIN913 M8x6
DIN913 M3x3
DIN912 M3x8
ISO7380 M3x10
BCN3DSigma-M07C01.0P01C Extruder clamp MK8
BCN3DSigma-M07C01.0P02D Extruder Holder MK8
BCN3DSigma-M07C01.0P03A Extruder plate MK8
BCN3DSigma-M07C01.0P04C Pneufit coupling
BCN3DSigma-M07C01.0P05C Extruder Stepper Holder
BCN3DSigma-M07C01.0P06B Extruder driver cover
BCN3DSigma-M07C01.0P08C Bowden entry extruder
BCN3DSigma-M07C01.0P10Z Nema 17 60mm
BCN3DSigma-M07C01.0P11Z Direct Drive Gear MK8
BCN3DSigma-M07C01.0P12Z Bearing 10-5-4
BCN3DSigma-M07C01.0P13A Extruder spring
BCN3DSigma-M07C01.0P19Z Coupling collet
BCN3DSigma-M07C01.0P15Z Bushing 3-6-10-1.5
BCN3DSigma-M07C01.0P16Z Bushing 3-6-5-1.5
BCN3DSigma-M07C01.0P17C Stepper insulator
BCN3DSigma-M07C01.0P18Z Clamp stop bushing
BCN3DSigma-M04C00.0P03E Stepper Driver Board
BCN3DSigma-M04C00.0P05Z Plastic spacer 3,2mm x 4
BCN3DSigma-M05C01.0P11B Driver spacer
Connexio cable pla 15 vies

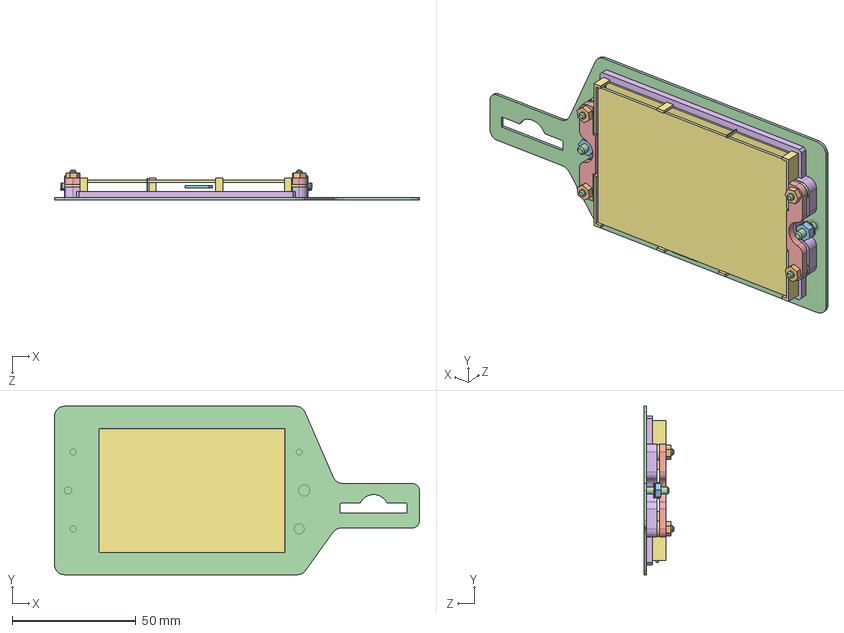
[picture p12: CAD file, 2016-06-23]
CAD/BCN3DSigma-M04C01.0P000 Screen.SLDASM
147.2 x 68.0 x 12.0 mm
DIN6798 M3 x 2
DIN934 M2,5 x 4
DIN934 M3 x 2
BCN3DSigma-M04C01.0P02C Screen Bezel
BCN3DSigma-M04C01.0P03B Back screen spacer x 2
BCN3DSigma-M04C01.0P04C Front screen spacer
BCN3DSigma-M04C01.0P05Z LCD Touchscreen
BCN3DSigma-M04C01.0P06Z Micro SD

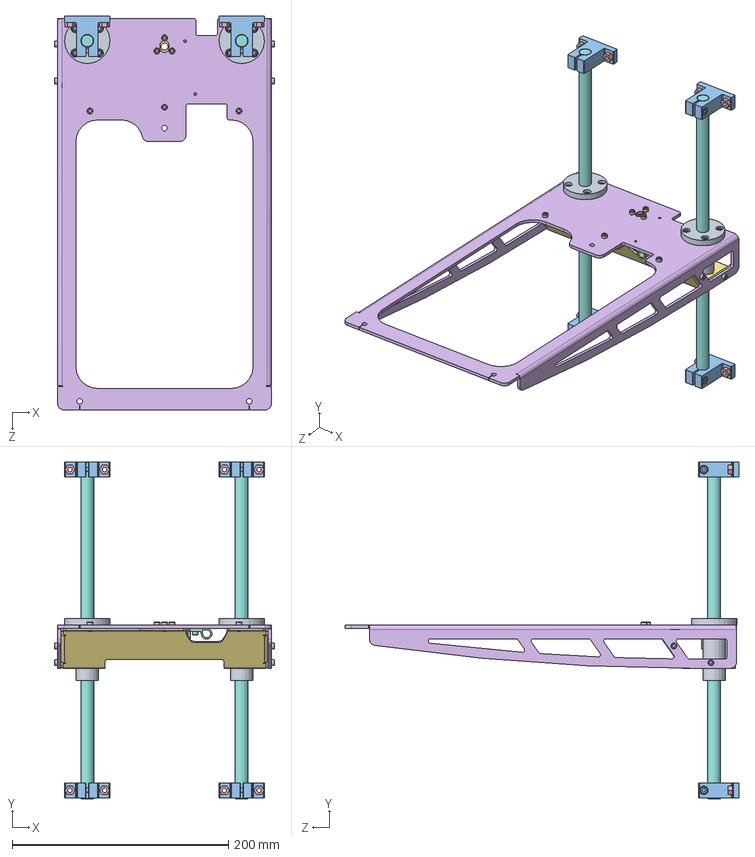
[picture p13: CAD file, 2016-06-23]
CAD/BCN3DSigma-M03C01.0P000 Z Axis structure.SLDASM
204.0 x 312.0 x 364.8 mm
DIN912 M3x6 x 17
DIN912 M3x8 x 3
DIN912 M4x12 x 4
DIN125 M3 x 8
DIN934 M5 x 8
BCN3DSigma-M03C01.0P01D Lower platform
BCN3DSigma-M03C01.0P02C Reinforcement
BCN3DSigma-M03C01.0P03B Z Bar x 2
BCN3DSigma-M03C01.0P04Z Flanged Linear Bushing x 2
BCN3DSigma-M03C01.0P05Z Z Nut
BCN3DSigma-M03C01.0P06Z Shaft Support x 4
BCN3DSigma-M01C01.0P13Z Hotbed cable clip x 2

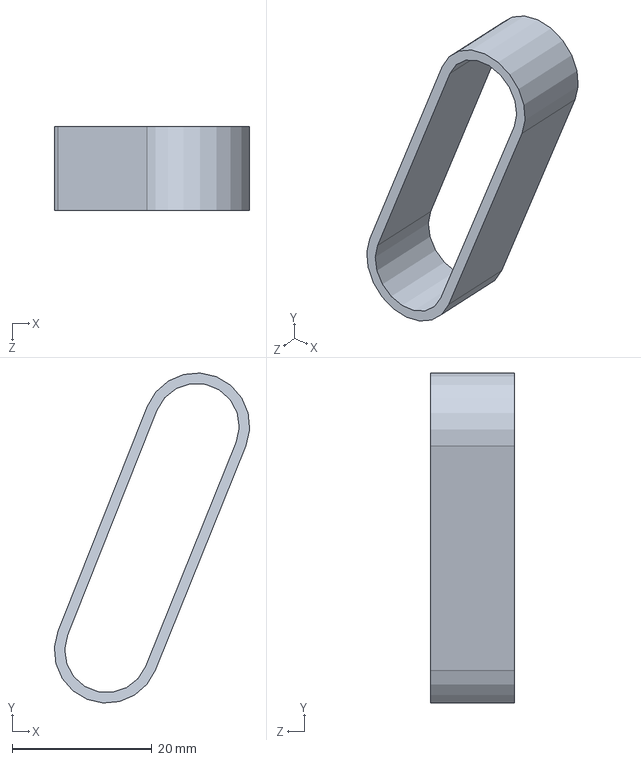
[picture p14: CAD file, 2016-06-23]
CAD/BCN3DSigma-M02C00.0P01Z Y Main Belt.sldprt
27.9 x 47.2 x 12.0 mm

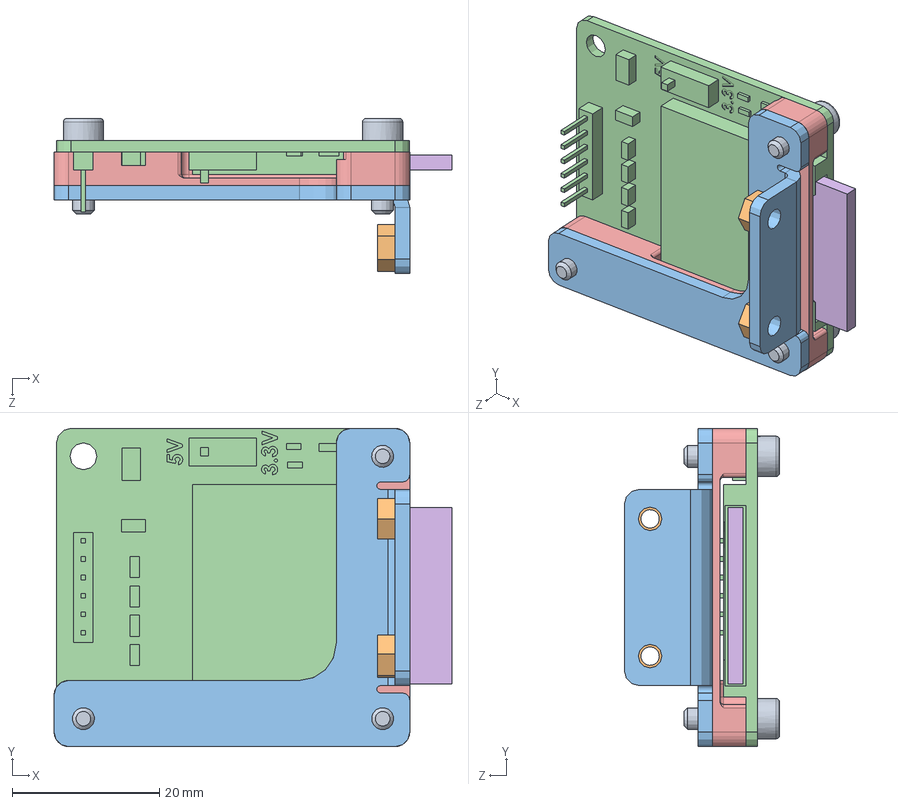
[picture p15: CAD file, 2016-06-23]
CAD/BCN3DSigma-M04C02.0P000 SD Unit.SLDASM
54.1 x 43.2 x 21.1 mm
DIN912 M3x10 x 3
DIN934 M3 x 2
BCN3DSigma-M04C02.0P01C SD Holder
BCN3DSigma-M04C02.0P02Z SD module
BCN3DSigma-M04C02.0P03A SD spacer
BCN3DSigma-M04C02.0P04Z SD Card 8GB

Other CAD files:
CAD/BCN3DSigma-M03C02.0P000 Printing surface.SLDASM
CAD/BCN3DSigma-M02C00.0P000 Y Axis.SLDASM
CAD/BCN3DSigma-M03C00.0P000 Z axis.SLDASM
CAD/BCN3DSigma-M05C02.0P000 X Axis Right.SLDASM
CAD/022012065.SLDPRT
CAD/022053061.SLDPRT
CAD/039014040.SLDPRT
CAD/BCN3DSigma-M01C00.0P000 Structure.SLDASM
CAD/BCN3DSigma-M01C01.0P02C Bottom frame.SLDPRT
CAD/BCN3DSigma-M01C01.0P03C Left side.SLDPRT
CAD/BCN3DSigma-M01C01.0P04C Right side.SLDPRT
CAD/BCN3DSigma-M01C01.0P05C Y Idler Tensioner.SLDPRT
CAD/BCN3DSigma-M01C01.0P06C Bowden exit.SLDPRT
CAD/BCN3DSigma-M01C01.0P07B Guide spacer.SLDPRT
CAD/BCN3DSigma-M01C01.0P08B Window.SLDPRT
CAD/BCN3DSigma-M01C01.0P11Z Power button.SLDPRT
CAD/BCN3DSigma-M01C01.0P12Z USB Extension Cable.SLDPRT
CAD/BCN3DSigma-M01C01.0P13Z Hotbed cable clip.SLDPRT
CAD/BCN3DSigma-M01C01.0P15A Square 90.SLDPRT
CAD/BCN3DSigma-M01C01.0P16A Square 60.SLDPRT
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

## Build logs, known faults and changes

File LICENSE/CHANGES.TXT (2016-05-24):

This file will hold all the changes made by the Licensees.

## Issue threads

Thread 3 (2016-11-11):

Missing printable part: Clamp for flat cable on extruder

mrcg, 2016-11-11:
I cannot find the clamp used for the extruder. See picture.
It's broken and i need to print new one.

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

Clamp seems to be mixture of items:
BCN3DSigma-M06C01.0P11B Cable Clip
+
BCN3DSigma-M06C01.0P13A Flat Cable Clip

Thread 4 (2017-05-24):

Missing Part > BCN3DSigma-Mechanics/CAD/ > Spool Holder and Spool.

rtrolle, 2017-05-24:

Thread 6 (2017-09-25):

CAD files for R17

WanaGo, 2017-09-25:
Hello,

Are the CAD files going to be released for the R17? Most things are the same as the R16 I know, but the BOM has differences, Can these please be updated?

thanks

WanaGo, 2019-04-07:
Bump

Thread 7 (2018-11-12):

Missing Filament End Stop Part/s

thesec, 2018-11-12:
The filament end stop parts seem missing from the BOM etc.
Could you add them please.

Prejkox, 2018-12-09:
+1

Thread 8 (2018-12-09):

CAD files need to be updated according to R19

Prejkox, 2018-12-09:

Prejkox, 2018-12-09:
CAD files for hotend, filament run-out sensor and new extruders can not be found in the CAD directory. There may be more things that have been updated on R19 that are not there.
Please update this.

WanaGo, 2019-04-07:
They are not even up to date for the R17. Please update these files.

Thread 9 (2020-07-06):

cad files show y stepper motor plate holding z stepper motor??

benjjyman, 2020-07-06:
I have an issue with heavy z ribbing caused by a wobbling z stepper, looked at cad drawings and although the z axis stepper mount matches the one fitted to my r17 the cad drawings use the Y axis stepper mount which looks more adjustable and better suited to the purpose.
Is this a file mistake and update or is my machine been fitted incorrectly ??

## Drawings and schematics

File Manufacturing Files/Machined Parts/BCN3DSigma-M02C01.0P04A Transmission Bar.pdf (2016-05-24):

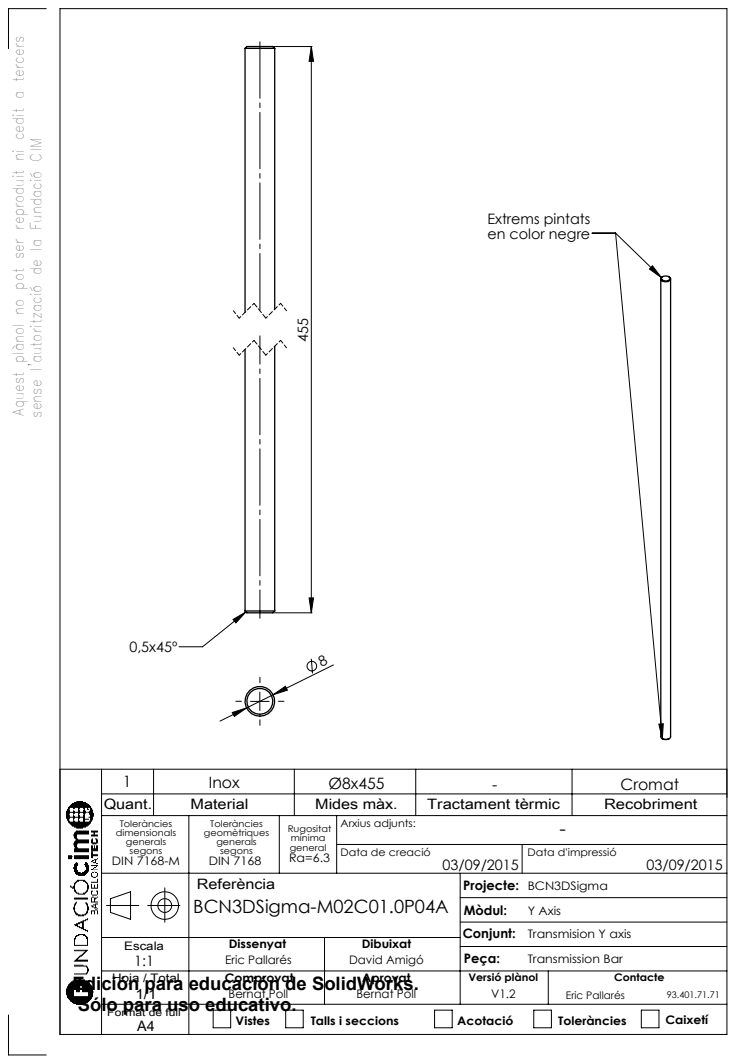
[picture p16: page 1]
Mides màx.; Tractament tèrmic; Recobriment; Data de creació; Data d'impressió; Vistes; Talls i seccions; Acotació; Toleràncies; Caixetí; Versió plànol; Bernat Poll; Transmission Bar; Eric Pallarés; - Cromat

Aquest plànol no pot ser reproduit ni cedit a tercers

sense l'autorització de la Fundació CIM

Extrems pintats
en color negre

Toleràncies dimensionals generals segons DIN 7168-M | Toleràncies geomètriques generals segons DIN 7168 | Rugositat mínima general Ra=6.3 | Arxius adjunts: | -

Referència BCN3DSigma-M02C01.0P04A | Projecte: BCN3DSigma Mòdul: Y Axis Conjunt: Transmision Y axis

Escala 1:1 | Dissenyat Eric Pallarés | Dibuixat David Amigó

Hoja / Total
Edición para educación de SolidWorks.
Sólo para uso educativo.
Format de full

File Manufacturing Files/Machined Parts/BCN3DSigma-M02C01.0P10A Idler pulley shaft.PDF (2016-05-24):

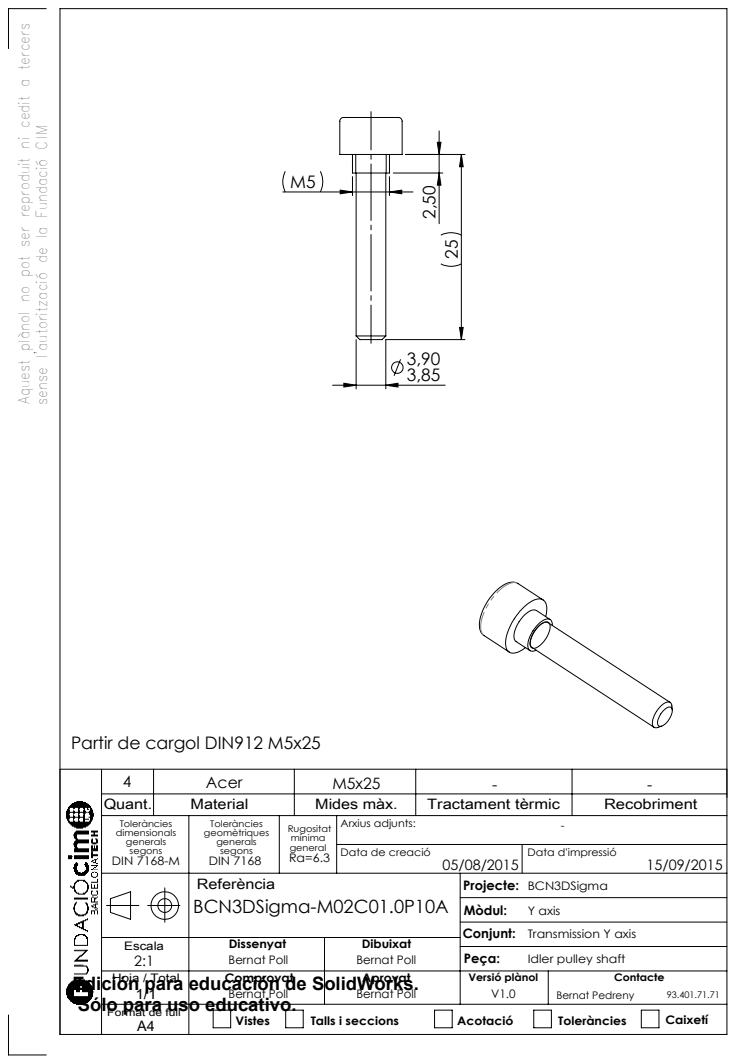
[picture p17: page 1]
Mides màx.; Tractament tèrmic; Recobriment; Data de creació; Data d'impressió; Vistes; Talls i seccions; Acotació; Toleràncies; Caixetí; Versió plànol; Bernat Poll; Bernat Pedreny

Aquest plànol no pot ser reproduit ni cedit a tercers

sense l'autorització de la Fundació CIM

Partir de cargol DIN912 M5x25
Quant.

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

Referència BCN3DSigma-M02C01.0P10A | Projecte: BCN3DSigma Mòdul: Y axis Conjunt: Transmission Y axis

Escala 2:1 | Dissenyat Bernat Poll | Dibuixat Bernat Poll

Idler pulley shaft

Hoja / Total
Edición para educación de SolidWorks.
Sólo para uso educativo.
Format de full

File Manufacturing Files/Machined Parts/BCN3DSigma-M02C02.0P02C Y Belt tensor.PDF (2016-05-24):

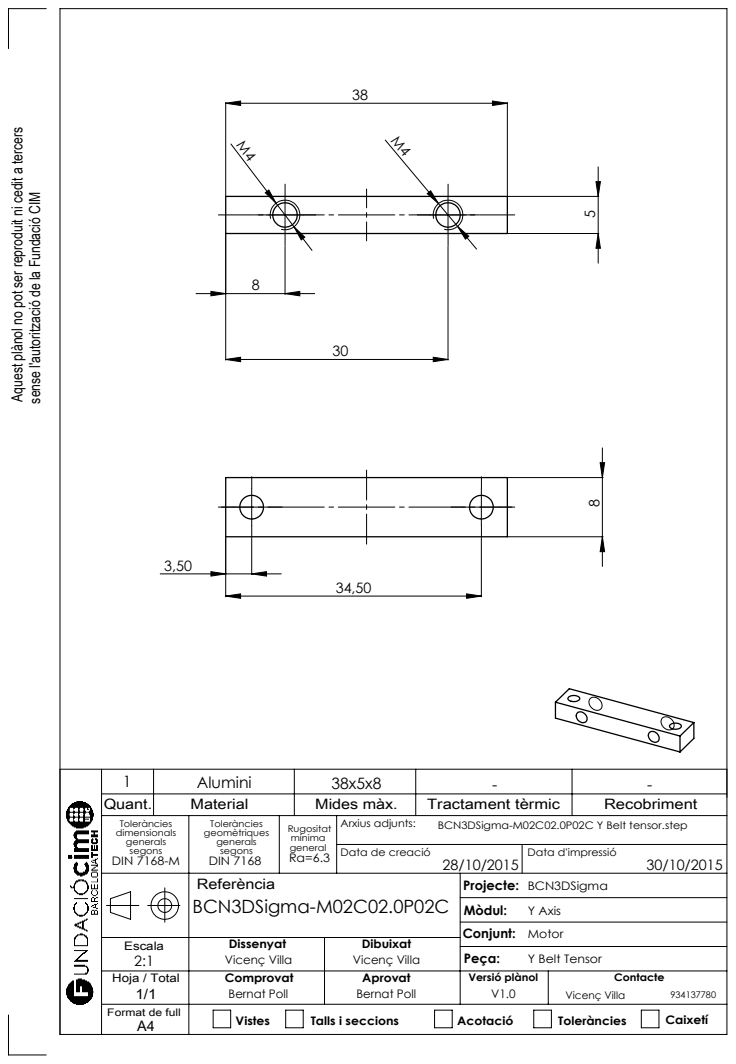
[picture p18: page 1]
Mides màx.; Tractament tèrmic; Recobriment; Data de creació; Data d'impressió; Vistes; Talls i seccions; Acotació; Toleràncies; Caixetí; Y Belt Tensor

Aquest plànol no pot ser reproduit ni cedit a tercers

sense l'autorització de la Fundació CIM

Toleràncies dimensionals generals segons DIN 7168-M | Toleràncies geomètriques generals segons DIN 7168 | Rugositat mínima general Ra=6.3 | Arxius adjunts: BCN3DSigma-M02C02.0P02C Y Belt tensor.step

Referència BCN3DSigma-M02C02.0P02C | Projecte: BCN3DSigma Mòdul: Y Axis Conjunt: Motor

Escala 2:1 | Dissenyat Vicenç Villa | Dibuixat Vicenç Villa

Hoja / Total 1/1 | Comprovat Bernat Poll | Aprovat Bernat Poll | Versió plànol V1.0 | Contacte Vicenç Villa 934137780

Format de full A4

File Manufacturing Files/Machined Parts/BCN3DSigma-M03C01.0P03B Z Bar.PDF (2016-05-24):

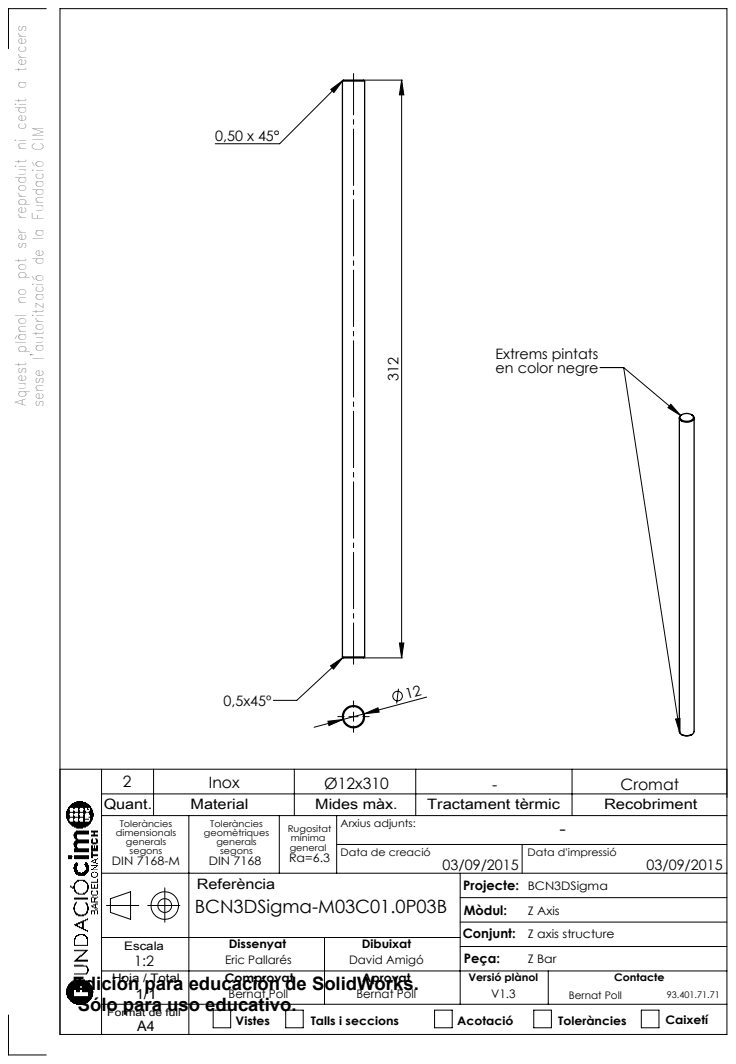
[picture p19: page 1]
Mides màx.; Tractament tèrmic; Recobriment; Data de creació; Data d'impressió; Vistes; Talls i seccions; Acotació; Toleràncies; Caixetí; Versió plànol; Bernat Poll; Z Bar; - Cromat

Aquest plànol no pot ser reproduit ni cedit a tercers

sense l'autorització de la Fundació CIM

Extrems pintats
en color negre

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

Referència BCN3DSigma-M03C01.0P03B | Projecte: BCN3DSigma Mòdul: Z Axis Conjunt: Z axis structure

Escala 1:2 | Dissenyat Eric Pallarés | Dibuixat David Amigó

Hoja / Total
Edición para educación de SolidWorks.
Sólo para uso educativo.
Format de full

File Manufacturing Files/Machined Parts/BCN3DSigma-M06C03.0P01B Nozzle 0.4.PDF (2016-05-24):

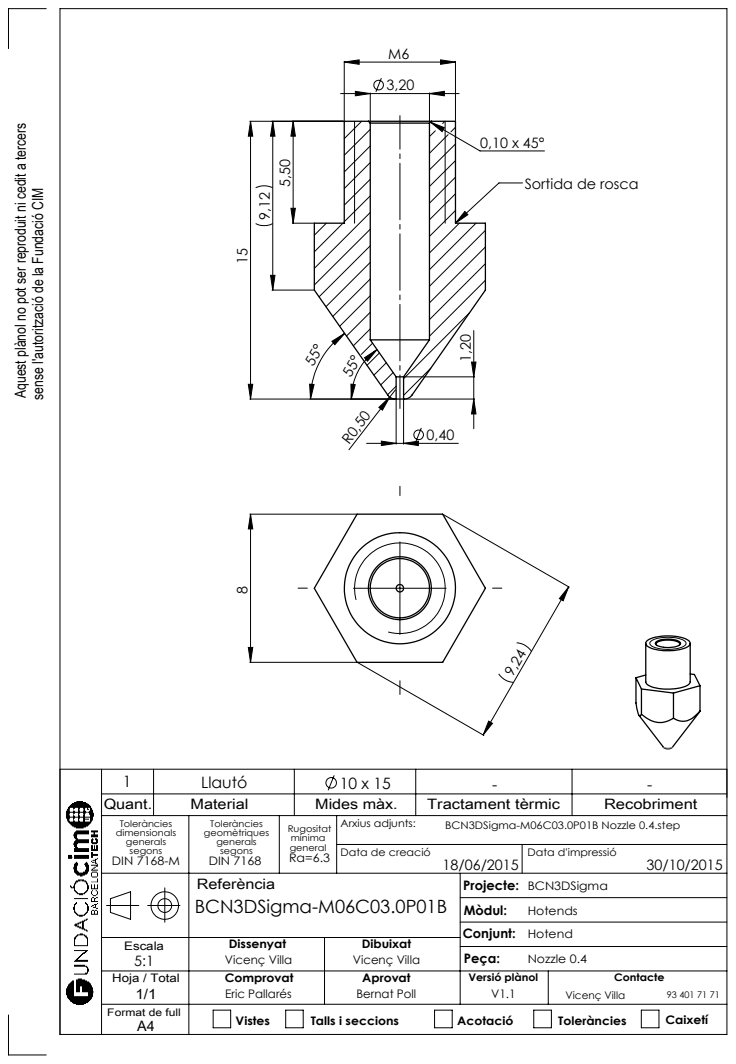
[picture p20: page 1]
Mides màx.; Tractament tèrmic; Recobriment; Data de creació; Data d'impressió; Vistes; Talls i seccions; Acotació; Toleràncies; Caixetí; Nozzle 0.4

Aquest plànol no pot ser reproduit ni cedit a tercers

Sortida de rosca

sense l'autorització de la Fundació CIM

Toleràncies dimensionals generals segons DIN 7168-M | Toleràncies geomètriques generals segons DIN 7168 | Rugositat mínima general Ra=6.3 | Arxius adjunts: BCN3DSigma-M06C03.0P01B Nozzle 0.4.step

Referència BCN3DSigma-M06C03.0P01B | Projecte: BCN3DSigma Mòdul: Hotends Conjunt: Hotend

Escala 5:1 | Dissenyat Vicenç Villa | Dibuixat Vicenç Villa

Hoja / Total 1/1 | Comprovat Eric Pallarés | Aprovat Bernat Poll | Versió plànol V1.1 | Contacte Vicenç Villa 93 401 71 71

Format de full A4

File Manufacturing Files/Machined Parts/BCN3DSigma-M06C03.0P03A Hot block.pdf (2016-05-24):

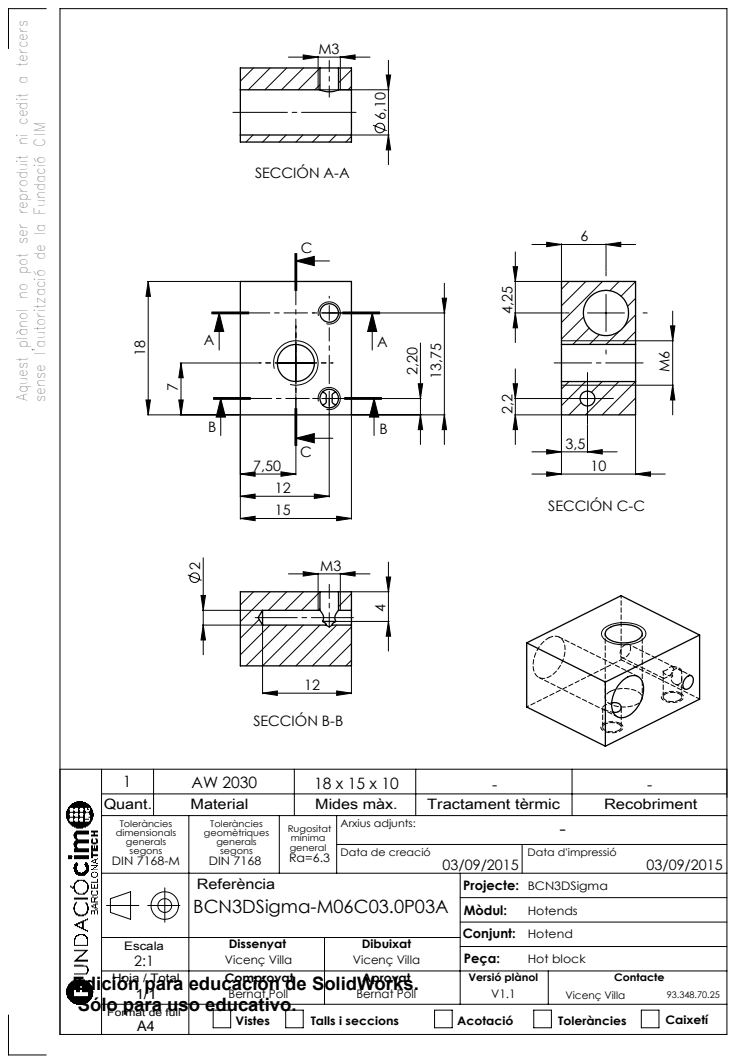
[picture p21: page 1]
Mides màx.; Tractament tèrmic; Recobriment; Data de creació; Data d'impressió; Vistes; Talls i seccions; Acotació; Toleràncies; Caixetí; Versió plànol; Bernat Poll; Hot block; Vicenç Villa; SECCIÓN A-A; SECCIÓN B-B; SECCIÓN C-C

Aquest plànol no pot ser reproduit ni cedit a tercers

sense l'autorització de la Fundació CIM

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

Referència BCN3DSigma-M06C03.0P03A | Projecte: BCN3DSigma Mòdul: Hotends Conjunt: Hotend

Escala 2:1 | Dissenyat Vicenç Villa | Dibuixat Vicenç Villa

Hoja / Total
Edición para educación de SolidWorks.
Sólo para uso educativo.
Format de full

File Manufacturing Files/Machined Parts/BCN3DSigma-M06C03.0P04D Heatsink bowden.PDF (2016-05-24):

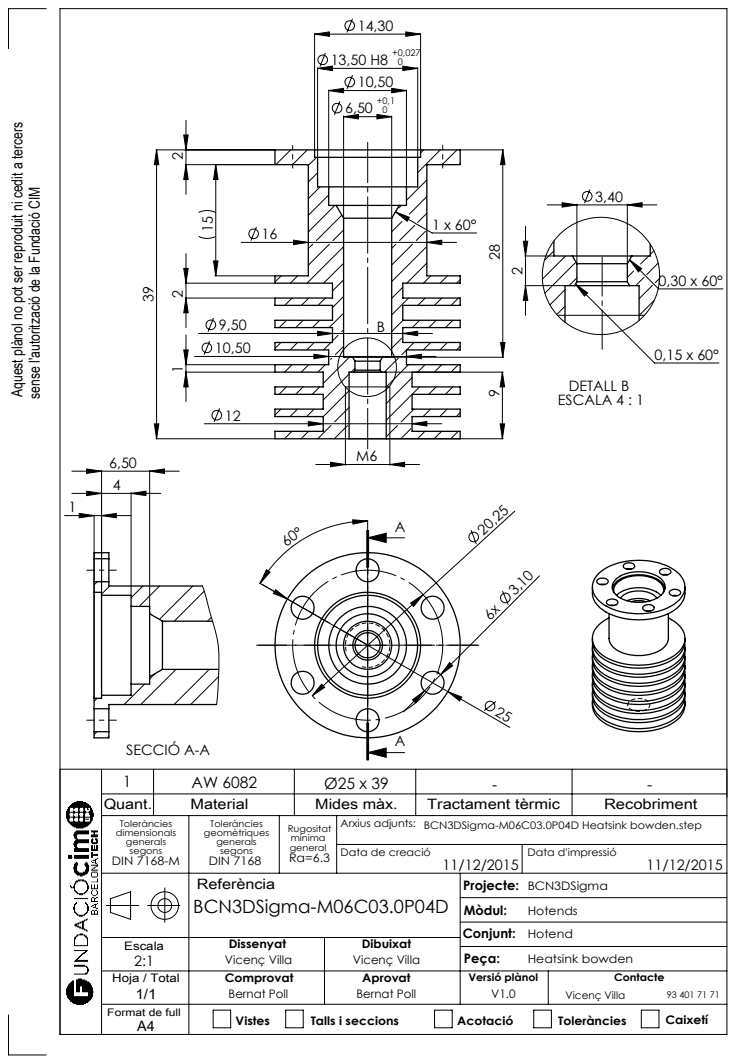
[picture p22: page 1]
Mides màx.; Tractament tèrmic; Recobriment; Data de creació; Data d'impressió; Vistes; Talls i seccions; Acotació; Toleràncies; Caixetí; Heatsink bowden; DETALL B ESCALA 4 : 1; SECCIÓ A-A

Aquest plànol no pot ser reproduit ni cedit a tercers

sense l'autorització de la Fundació CIM

Toleràncies dimensionals generals segons DIN 7168-M | Toleràncies geomètriques generals segons DIN 7168 | Rugositat mínima general Ra=6.3 | Arxius adjunts: BCN3DSigma-M06C03.0P04D Heatsink bowden.step

Referència BCN3DSigma-M06C03.0P04D | Projecte: BCN3DSigma Mòdul: Hotends Conjunt: Hotend

Escala 2:1 | Dissenyat Vicenç Villa | Dibuixat Vicenç Villa

Hoja / Total 1/1 | Comprovat Bernat Poll | Aprovat Bernat Poll | Versió plànol V1.0 | Contacte Vicenç Villa 93 401 71 71

Format de full A4

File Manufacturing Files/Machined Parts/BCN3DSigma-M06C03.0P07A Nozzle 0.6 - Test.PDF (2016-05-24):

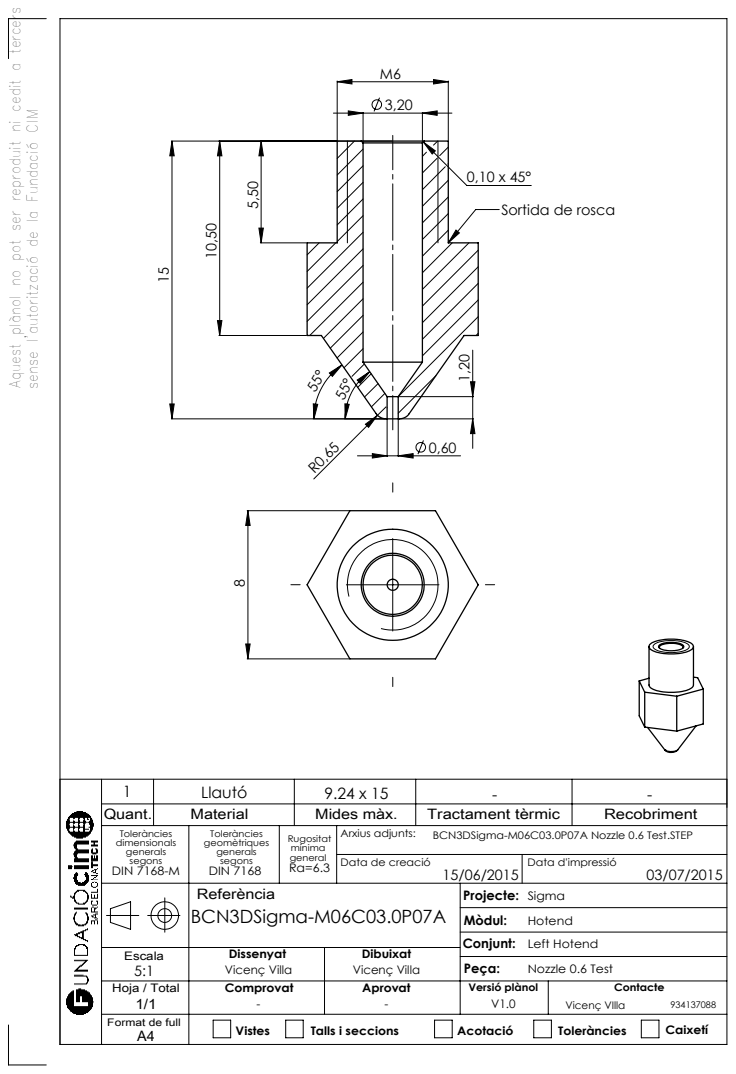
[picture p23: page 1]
Mides màx.; Tractament tèrmic; Recobriment; Data de creació; Data d'impressió; Vistes; Talls i seccions; Acotació; Toleràncies; Caixetí; Nozzle 0.6 Test

Aquest plànol no pot ser reproduit ni cedit a tercers

sense l'autorització de la Fundació CIM

Sortida de rosca

Toleràncies dimensionals generals segons DIN 7168-M | Toleràncies geomètriques generals segons DIN 7168 | Rugositat mínima general Ra=6.3 | Arxius adjunts: BCN3DSigma-M06C03.0P07A Nozzle 0.6 Test.STEP

Referència BCN3DSigma-M06C03.0P07A | Projecte: Sigma Mòdul: Hotend Conjunt: Left Hotend

Escala 5:1 | Dissenyat Vicenç Villa | Dibuixat Vicenç Villa

Hoja / Total 1/1 | Comprovat - | Aprovat - | Versió plànol V1.0 | Contacte Vicenç VIlla 934137088

Format de full A4

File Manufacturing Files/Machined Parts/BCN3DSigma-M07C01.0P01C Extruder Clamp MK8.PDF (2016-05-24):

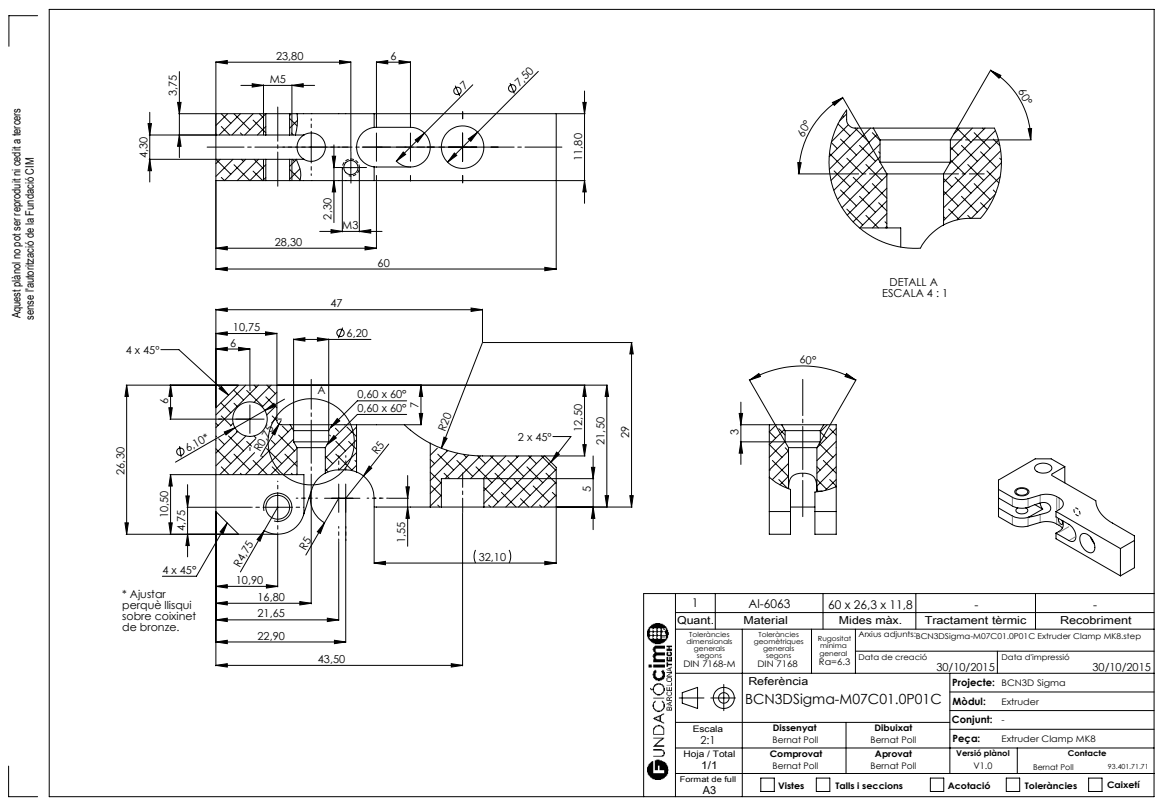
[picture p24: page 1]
Mides màx.; Tractament tèrmic; Recobriment; Data de creació; Data d'impressió; Vistes; Talls i seccions; Acotació; Toleràncies; Caixetí; Extruder Clamp MK8; DETALL A ESCALA 4 : 1; * Ajustar perquè llisqui sobre coixinet de bronze.

Aquest plànol no pot ser reproduit ni cedit a tercers

sense l'autorització de la Fundació CIM

Toleràncies dimensionals generals segons DIN 7168-M | Toleràncies geomètriques generals segons DIN 7168 | Rugositat mínima general Ra=6.3 | Arxius adjunts: BCN3DSigma-M07C01.0P01C Extruder Clamp MK8.step

Referència BCN3DSigma-M07C01.0P01C | Projecte: BCN3D Sigma Mòdul: Extruder -Conjunt:

Escala 2:1 | Dissenyat Bernat Poll | Dibuixat Bernat Poll

Hoja / Total 1/1 | Comprovat Bernat Poll | Aprovat Bernat Poll | Versió plànol V1.0 | Contacte Bernat Poll 93.401.71.71

Format de full A3

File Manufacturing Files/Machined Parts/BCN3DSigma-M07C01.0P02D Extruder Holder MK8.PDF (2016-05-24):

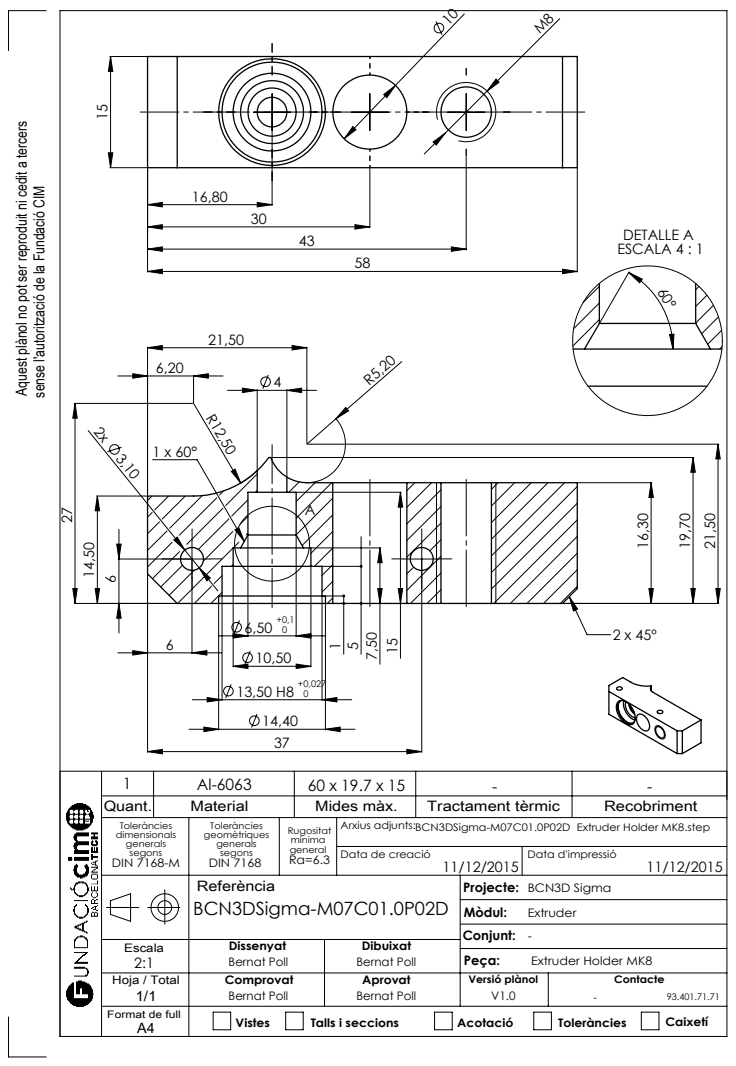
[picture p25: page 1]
Mides màx.; Tractament tèrmic; Recobriment; Data de creació; Data d'impressió; Vistes; Talls i seccions; Acotació; Toleràncies; Caixetí; Extruder Holder MK8; DETALLE A ESCALA 4 : 1

Aquest plànol no pot ser reproduit ni cedit a tercers

sense l'autorització de la Fundació CIM

Toleràncies dimensionals generals segons DIN 7168-M | Toleràncies geomètriques generals segons DIN 7168 | Rugositat mínima general Ra=6.3 | Arxius adjunts: BCN3DSigma-M07C01.0P02D Extruder Holder MK8.step

Referència BCN3DSigma-M07C01.0P02D | Projecte: BCN3D Sigma Mòdul: Extruder Conjunt: -

Escala 2:1 | Dissenyat Bernat Poll | Dibuixat Bernat Poll

Hoja / Total 1/1 | Comprovat Bernat Poll | Aprovat Bernat Poll | Versió plànol V1.0 | Contacte -93.401.71.71

Format de full A4

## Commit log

2016-05-24 Added Files to the repository
    Added the main files to the repository
    [022053061.SLDPRT, BCN3DSigma-M01C00.0P000 Structure.SLDASM, BCN3DSigma-M01C01.0P02C Bottom frame.SLDPRT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]
2016-05-24 Add Full assembly compressed
2016-06-23 New CAD files with fixed References
    Fixed the references error with folders and stuff
    [022012065.SLDPRT, 022053061.SLDPRT, 039014040.SLDPRT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]
2016-06-23 Added BOM in pdf format
    Added Bill of Materials of the BCN3D Sigma
2017-01-31 Added missing part - Hotend Plate
    [BCN3DSigma-M06C01.0P07D Hotend Plate.SLDPRT]
